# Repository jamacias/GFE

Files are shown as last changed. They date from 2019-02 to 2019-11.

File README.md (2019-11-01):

# GFE
Güimar Farm Explorer (GFE) is a low cost autonomous rover that aims at performing assisting and supervising remote farms.

The idea of the project is to be able to monitor a farm by commanding the robot to go to a certain known position and perform certain tasks of interest without having a human to be physically on site. Interesting uses may be related to crop health monitoring using NDVI images, apart from actually harvesting fruits (hopefully!).

The most recent version, iteration 2, is based on ["The bubble rebound obstacle avoidance algorithm"](https://ieeexplore.ieee.org/document/5524302). An array of ultrasonic sensors measure the distance to the objects and if any threat is detected the robot moves navigates on the direction with less density of obstacles. This project is designed to be used in semi-structured environments where the map and the way points that are (most probably) free of obstacles are known. The morphology and motion implemented kept in mind that it is designed to work in a winery with limited space, thus high agility is desired.

Please, refer to Thesis.pdf, images and the rest of the documentation inside the project itself for more information. Note that some of these are written in Spanish as this is the final project of my BSc. in Electronic Engineering. Nevertheless, all the source code is in English.

<p align="center">
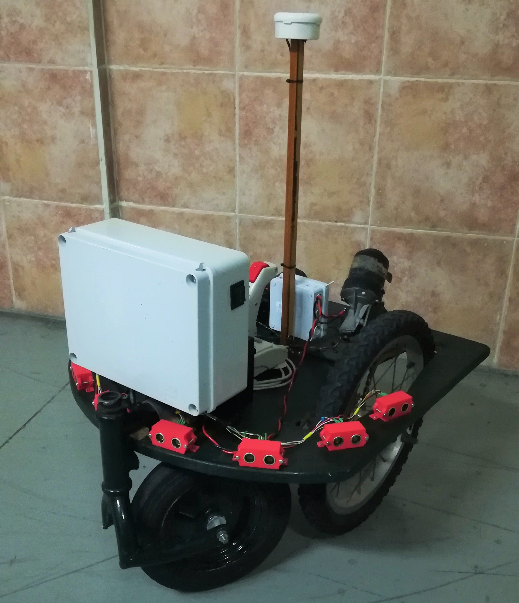
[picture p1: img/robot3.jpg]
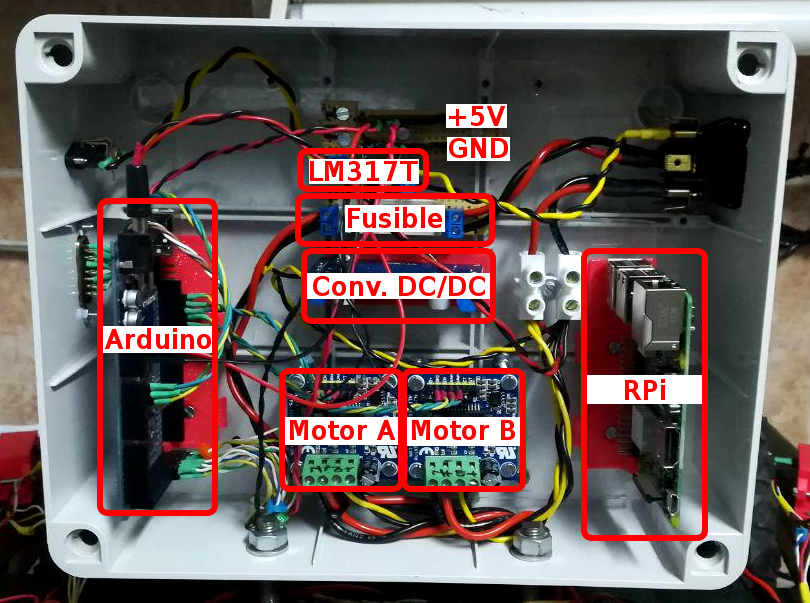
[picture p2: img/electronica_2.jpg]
     
</p>

## Main features:
- Manual control of the robot using diamond coordinates with a Quickshot QS-203 joystick.
- Autonomous navigation through waypoints marked.
- Obstacle avoidance.
- PI controller for the orientation of the robot.

## Known issues:
- Poor robustness on windy conditions - ultrasonic sensors are very sensible to this noise.
- Lack of sensor fusion for higher accuracy, nor Kalman filtering. Thus, kinematic equations are not really considered.
- Lack of encoders to compensate the shift between the wheels. This is compensated by transforming the system from MISO to SISO by using the orientation as the objective and setting the same values to both motors.
- No continuous trajectory is designed. The vehicle enters on either uses a PI controller to rotate to the correct orientation, or just moves forward in such direction. Considering the orography of the terrain where it was conceived, this might be a constraint anyway.

Even though these issues exist, the robot performs relatively well under certain conditions. It is able to navigate to the desired point with relatively good accuracy. The obstacle avoidance also works well under indoor conditions where the disturbance of the wind is minimal.

## BOM:
- Arduino MEGA 2560.
- Raspberry PI.
- 2x Windshield wiper DC motors (TGE5889A).
- 2x IMS-1 motor driver modules.
- 8x Ultrasonic sensors HC-SR04.
- 12V battery.
- LM317T voltage regulator.
- HMC5883L magnetometer.
- GY-GPS6MV2 GPS.
- Quickshot QS-203 joystick.
- Raspberry Pi NoIR camera.

## Libs:
- MOTOR (IMS-1 motor driver) - can be found in libs.
- TinyGPS.
- HMC5883_Simple.

## References:
[NDVI with RPi](https://github.com/robintw/RPiNDVI)

["The bubble rebound obstacle avoidance algorithm"](https://ieeexplore.ieee.org/document/5524302)

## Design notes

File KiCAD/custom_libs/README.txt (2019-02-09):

All libs are own-made except:

 -HC-SR04 https://github.com/adamclaassen/adamclaassen-kicad-parts (Modified: aesthetics)
 -ESP8266 https://github.com/jdunmire/kicad-ESP8266 (Modified: aesthetics)

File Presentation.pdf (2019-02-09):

# Diseño electrónico de un robot autónomo

## Trabajo de Fin de Grado

Javier Macías Solá
Universidad de La Laguna - GIEIA | Tutor: Dr. Leopoldo Acosta Sánchez

## Índice

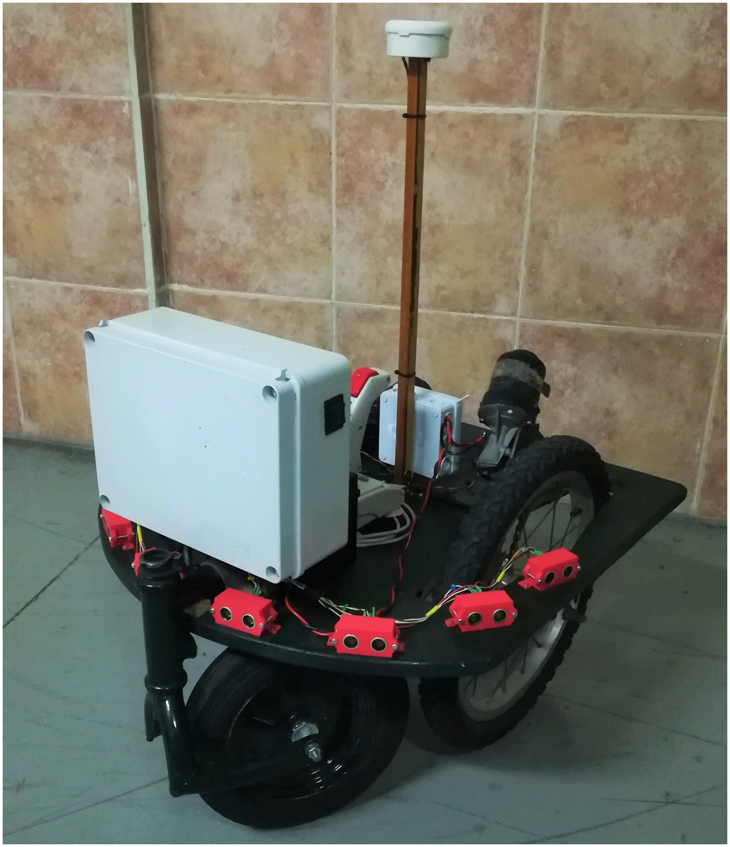
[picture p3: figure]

1. Introducción.
a. Objetivos.
b. Punto de partida.
2. Estudio previo y bases de diseño.
a. Concepto básicos de robots móviles.
b. Cinemática.
3. Electrónica. Sensores y actuadores.
4. Implementaciones.
a. Resumen versión 1.
b. Versión 2: modificaciones.
i. Estructura.
ii. Software.
5. Conclusions.

## Introducción

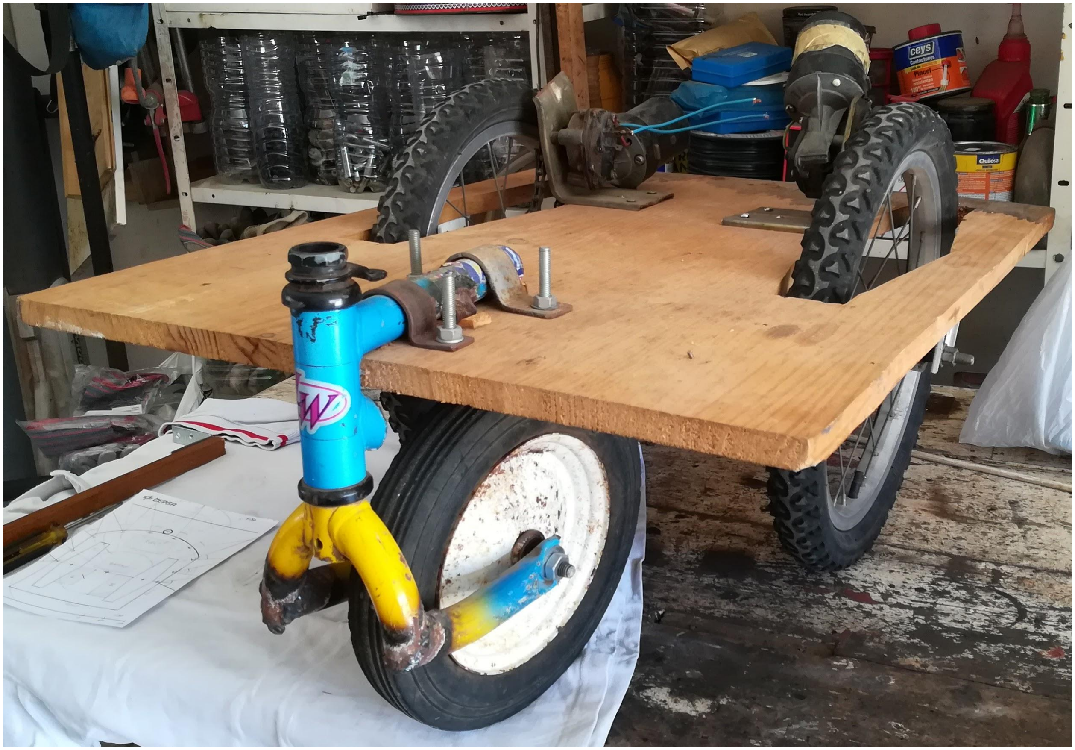
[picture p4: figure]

Idea: navegación autónoma entre los puntos marcados en un mapa desde una interfaz.

1. Objetivos básicos
a. Control autónomo y manual
b. Evitar obstáculos
2. Punto de partida
a. Base cuadrada (50 x 70 cm)
b. Dos ruedas diferenciales y una loca

# Estudio previo y bases de diseño

## Estudio previo

Robot móvil: tres grados de libertad (x, y, θ) con respecto al mundo global.

Navegación: conocer la ubicación actual, idear, y seguir una ruta.

1. Localización: ¿dónde está el robot?
a. Orientación limitada al rango [0, 360) grados.
b. Localización en grados decimales. Más cifras, más precisión y ruido.
2. Planificación: ¿ruta libre de obstáculos?

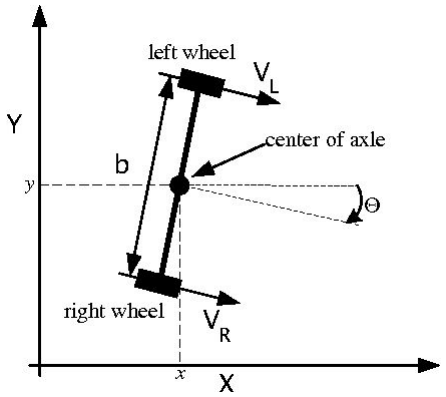
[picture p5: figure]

Fuente: Semantic Scholar

## Estudio previo

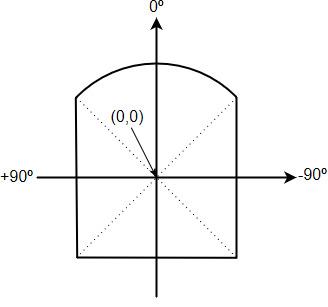
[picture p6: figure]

Coordenadas locales:

1. Origen en el centro geométrico.
2. Cero grados frente del vehículo, eje y. El signo del ángulo determina el lado.

¿Se puede ubicar un sensor?

Cinemática: depende de la velocidad y dirección de giro de las ruedas laterales.

## Bases de diseño

1. Maniobrabilidad
2. Detectar y evitar obstáculos
3. Poco volumen (radio < 1 m), pasillos de 1.40 m
4. Bajo costo/modular
5. Centro de gravedad bajo, estabilidad
6. Espacio para futuras mejoras
7. Escalabilidad

# Electrónica

Sensores y actuadores

## Electrónica general

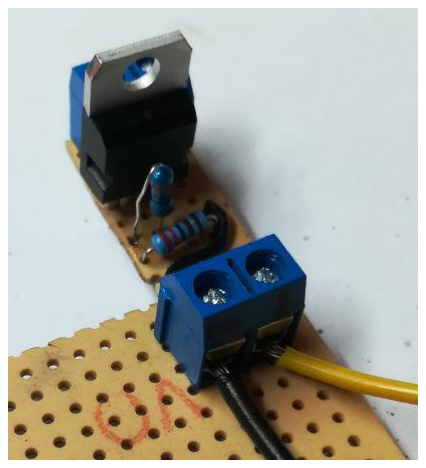
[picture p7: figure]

1. Batería: aporta la energía al sistema.
a. Reciclada de una moto.
b. Química: plomo ácido.
c. Seis celdas, 2.1 voltios por celda, 12.6 V total (OCV).
d. Ventaja: voltaje seguro y típico. En OCV representa el nivel de carga.
2. Cargador: fuente que permite recargar la batería.
a. Invierte la reacción química.
b. Plomo ácido: voltaje de carga entre 2.3 y 2.4 V/celda.
c. Reutilizada de un equipo de 17 V, adaptar el voltaje.
d. Polarizar un regulador (LM317T) a 13.8 V.
i. Dropout voltage ≈ 3.2 V.
ii. Intensidad máxima: 2.2 A.

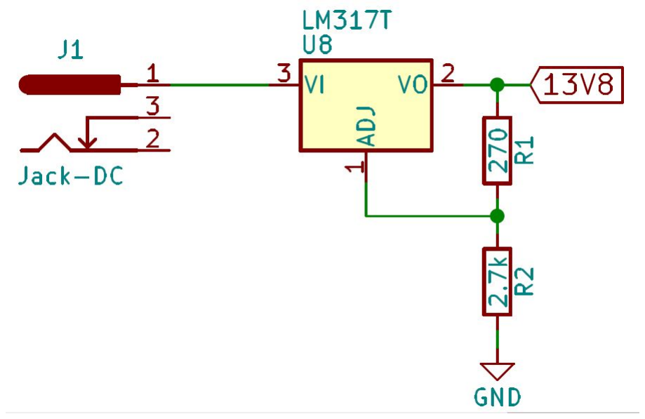
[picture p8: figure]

## Electrónica general

3. Controlador - Arduino MEGA 2560
a. Alimentación a 12 V con regulador integrado.
b. 4x Puertos Serial.
c. 2x I2C.
d. 15x PWM.
e. 16x Entradas analógicas.
f. 15x I/O digitales.
g. 10 bits ADC.
h. 8 bits DAC.
i. C/C++

No aporta potencia, hasta 20 mA/pin.

## Sensores

Permiten cerrar el lazo de realimentación del sistema.

1. Brújula: orientación del robot midiendo el campo magnético terrestre.
a. Orientación y ubicación críticas.
b. Separación de objetos metálicos (radio > 30 cm).
c. Librería: HMC5883_Simple.
d. Calibrar el módulo según la declinación magnética.
e. GY-271, magnetómetro HMC5883L
i. Alimentación a 5 V.
ii. Comunicación I2C.

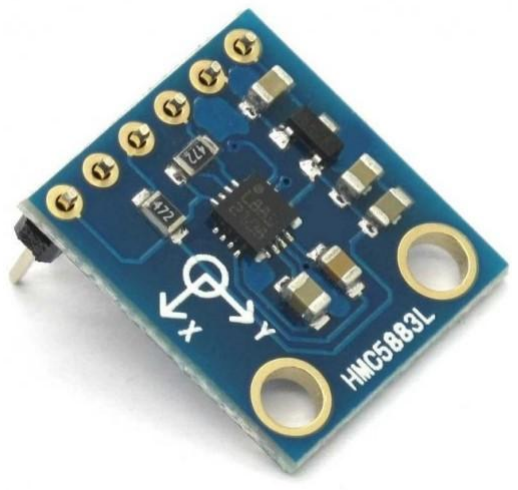
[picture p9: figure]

Fuente: njuskalo.hr

## Sensores

2. GPS: ubicación con respecto al mundo global.
a. Latitud (y) y longitud (x).
b. Librería: TinyGPS.
c. GY-GPS6MV2.
i. Alimentación a 5 V.
ii. Comunicación Serial.
d. Parsear sentencias típicas y estándar.
e. Señales débiles.

Fuente: dx.com

Ejemplo: $GPRMC,032606,A,3410.2358,N,11819.0865,W,0.0,207.2,180211,13.5,E,A*32

## Sensores

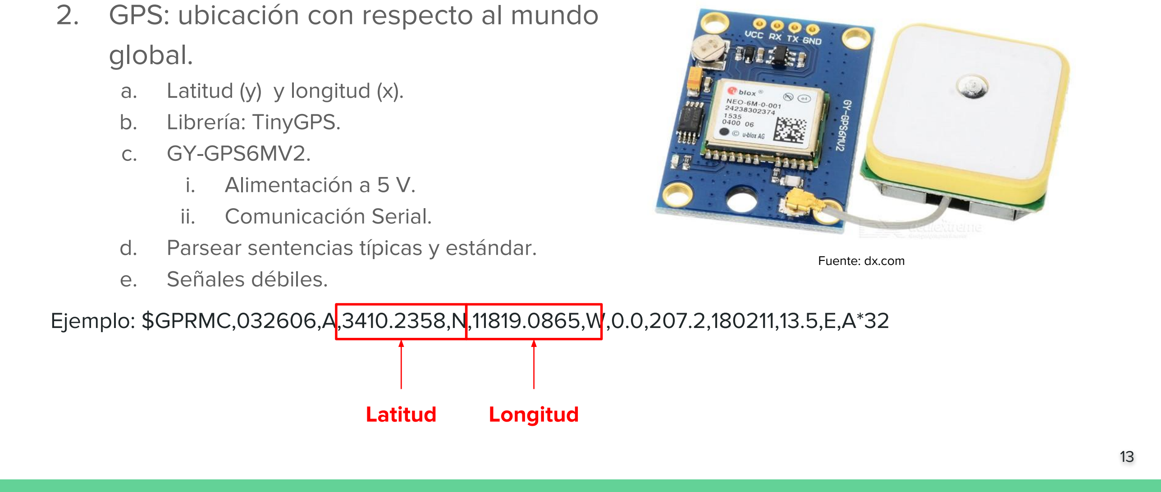
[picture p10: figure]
2. GPS: ubicación con respecto al mundo global.; a. Latitud (y) y longitud (x). b. Librería: TinyGPS. c. GY-GPS6MV2. i. Alimentación a 5 V.; Comunicación Serial.; e. Señales débiles.; Fuente: dx.com; Latitud; Longitud

d. Parsear sentencias típicas y estándar.

Ejemplo: $GPRMC,032606,A,3410.2358,N,11819.0865,W,0.0,207.2,180211,13.5,E,A*32

## Sensores

3. Ultrasonidos: detectar obstáculos.
a. Ventajas:
i. No hace falta librería. Función propia. ii. Económicos.
b. Desventajas:
i. Ondas de presión.
ii. | Eco
iii. | Escasa resolución espacial.
c. HC-SR04:
i. Alimentación a 5 V.
ii. | Comunicación por pines echo y trig.
iii. | Apertura de 15 grados.
iv. | Frecuencia máxima: 20 Hz

Fuente: amazon.co.uk

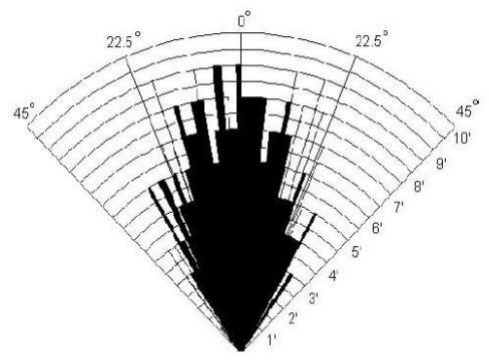
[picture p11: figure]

Fuente: [25]

## Sensores

4. Joystick: control manual del operario.
a. Manejo intuitivo.
b. Dos potenciómetros que marcan cada eje.
c. Adaptar Quickshot QS-203:
i. Potenciómetros polarizados a 5 V y lectura del valor analógico.
ii. | Pull-up resistors para los botones.
iii. | Trimado.
iv. | Mantener el conector DA-15.

## Adaptación joystick

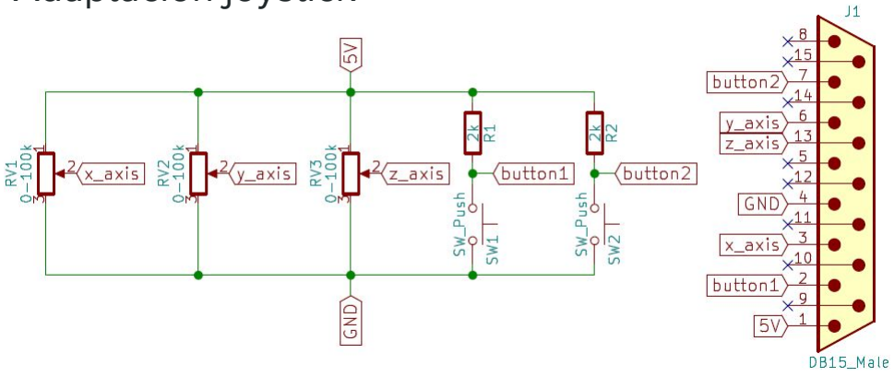
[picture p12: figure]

## Actuadores

1. Motores: cambian la pose del vehículo.
a. TGE589A. Motor de limpiaparabrisas.
i. DC, velocidad proporcional al voltaje.
ii. | Tornillo sin fin, par alto (18.3 Nm).
iii. | Consumo: 0.9 A con poca carga.
iv. | Intensidad de cortocircuito: 12 A.
v. Velocidad angular: 66 rpm.
b. Desventajas: falta de documentación.
c. Reductora externa de 8/16.

Suponiendo correctos los datos anteriores: hasta 176 kg con dos motores.

Fuente: rctankcombat.com

Solución: puente H excitado con PWM.

Módulo IMS-1

a. Hasta 50 A.
b. Velocidad de 8 bits (DAC Arduino).
c. Librería: MOTOR.

## Problema: voltaje intermedio en un sistema digital

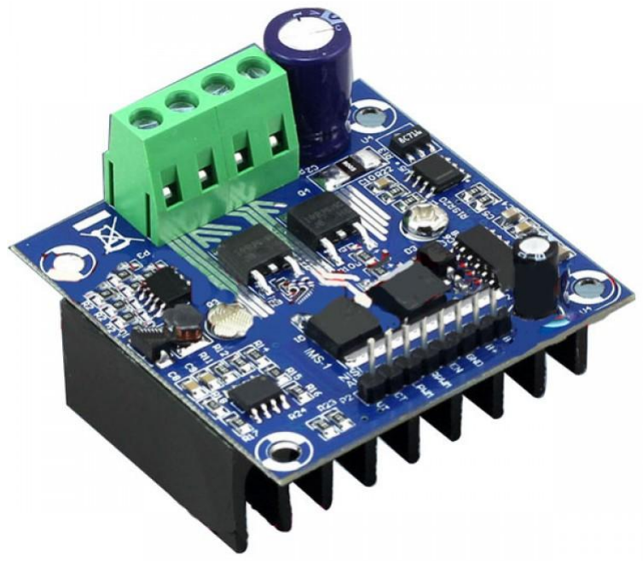
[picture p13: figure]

Fuente: thanksbuyer.com

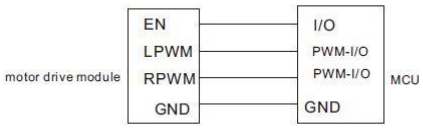
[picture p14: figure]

Fuente: [10]

# Implementaciones

Centrada en implementar los componentes.

a. Modo automático:
i. Orientado a seguir un rumbo y evitar paredes.
ii. | Cuatro sensores ultrasonidos.
iii. | Controlador todo/nada.
b. Modo manual:
i. Algoritmo: transformar coordenadas cartesianas a
| diamante y comandar los motores.
c. Problemas:
i. Orientación y comunicación remota poco robusta. ii. Inercia. Centro de gravedad desplazado.

## Resumen versión 1

## Resumen versión 1

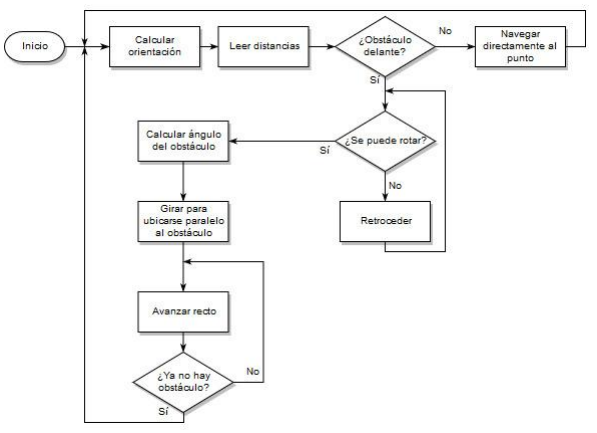
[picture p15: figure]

## Resumen versión 1

Algoritmo modo manual: transformar coordenadas cartesianas a diamante [23].

## Resumen versión 1

## Resumen versión 1

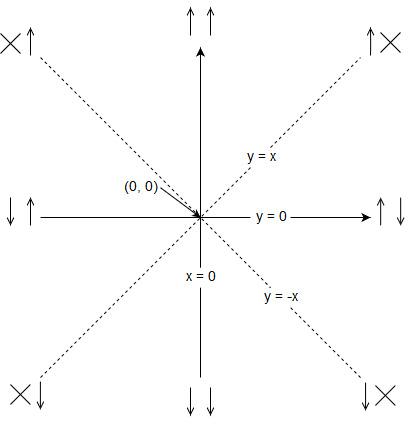
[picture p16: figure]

## Resumen versión 1

Fuente: [23]

## Resumen versión 1

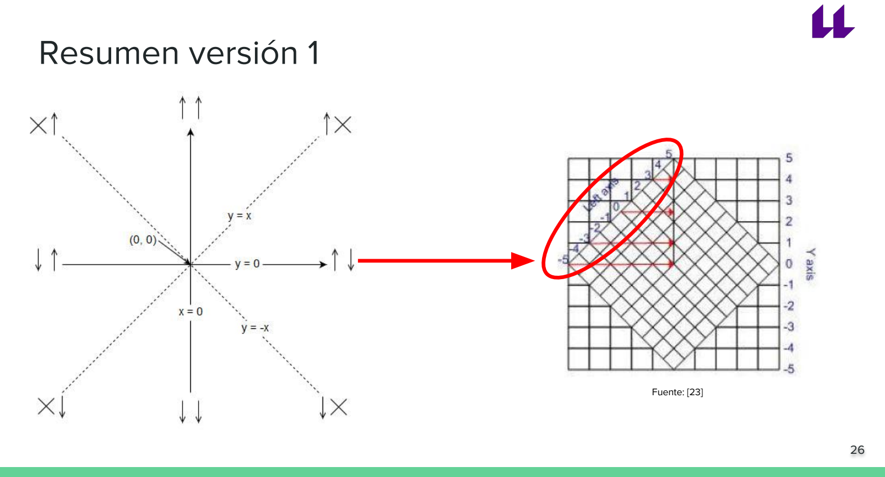
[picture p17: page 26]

Fuente: [23]

Implementar navegación y evitar obstáculos.

1. Electrónica jerárquica: multi-threading.
2. Centro de gravedad menos desplazado.
3. “The bubble rebound obstacle avoidance algorithm” [22].
4. Protecciones para sensores y nuevas ubicaciones.
5. Controlador PI.

## Versión 2: modificaciones

## Versión 2: electrónica

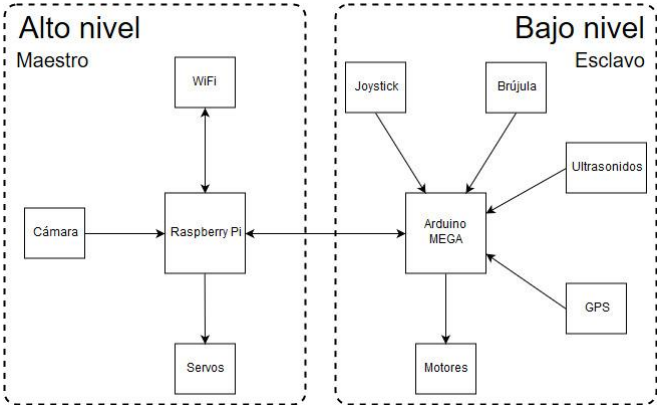
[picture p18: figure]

## Versión 2: electrónica

1. Brújula.
2. Joystick.
3. Motores.
4. GPS.
5. Interruptor de tres estados.
6. Batería.
7. Interfaces de comunicación.
8. Resto de electrónica.
9. Array de ultrasonidos.

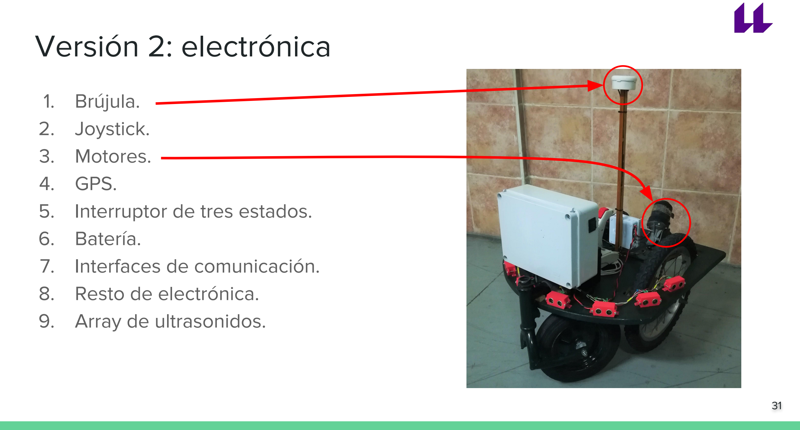
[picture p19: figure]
Versión 2: electrónica; 1. Brújula. 2. Joystick. 3. Motores. 4. GPS. 5. Interruptor de tres estados. 6. Batería. 7. Interfaces de comunicación. 8. Resto de electrónica. 9. Array de ultrasonidos.

## Versión 2: electrónica

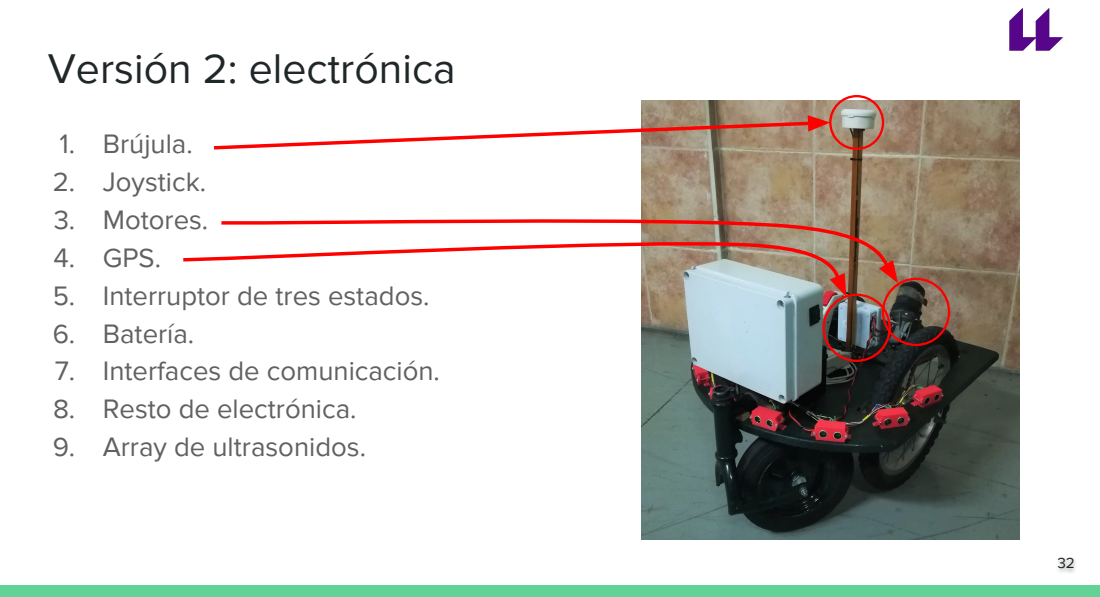
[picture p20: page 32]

1. Brújula.
2. Joystick.
3. Motores.
4. GPS.
5. Interruptor de tres estados.
6. Batería.
7. Interfaces de comunicación.
8. Resto de electrónica.
9. Array de ultrasonidos.

## Versión 2: electrónica

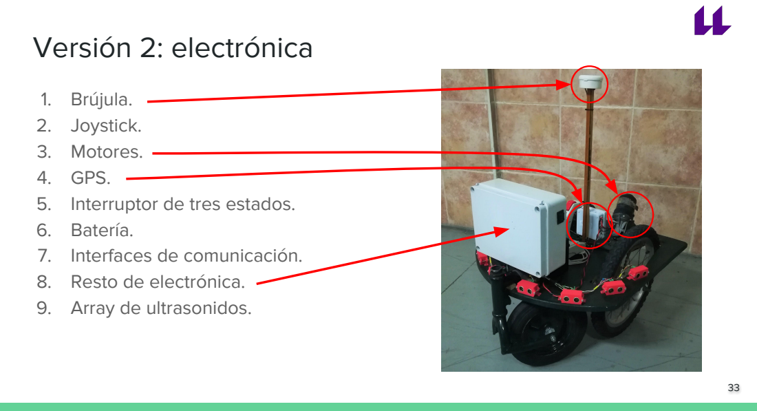
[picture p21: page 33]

1. Brújula.
2. Joystick.
3. Motores.
4. GPS.
5. Interruptor de tres estados.
6. Batería.
7. Interfaces de comunicación.
8. Resto de electrónica.
9. Array de ultrasonidos.

## Versión 2: electrónica

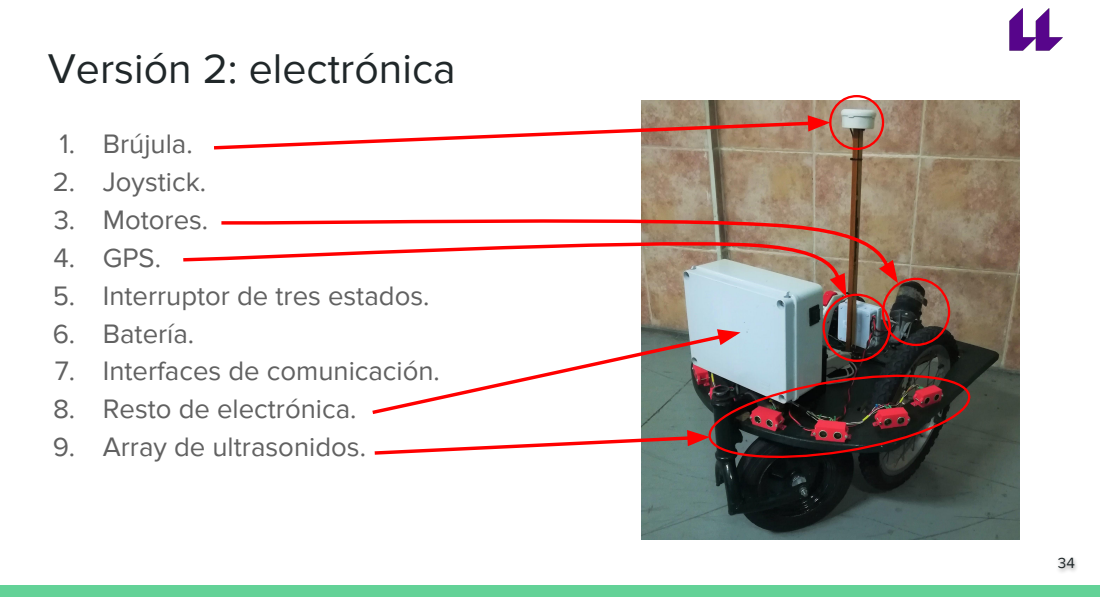
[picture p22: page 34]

1. Brújula.
2. Joystick.
3. Motores.
4. GPS.
5. Interruptor de tres estados.
6. Batería.
7. Interfaces de comunicación.
8. Resto de electrónica.
9. Array de ultrasonidos.

## Versión 2: electrónica

DC jack cargador.

Conector DA-15 (joystick).

Gestionar la comunicación remota. Alto nivel.

1. AP para conexión SSH.
2. Tiempo de arranque lento.
3. GPIOs configurados en boot (bash).
4. Alias de Linux para cambiar el estado.
5. Comunicación Serial con Arduino (debug).

Versión 2: software. Raspberry Pi.

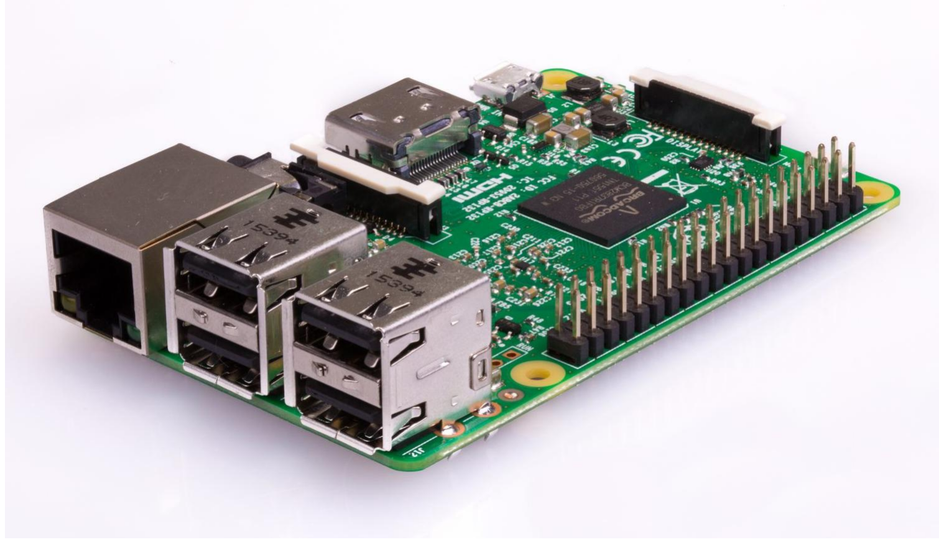
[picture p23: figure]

Fuente: raspberrypi.org

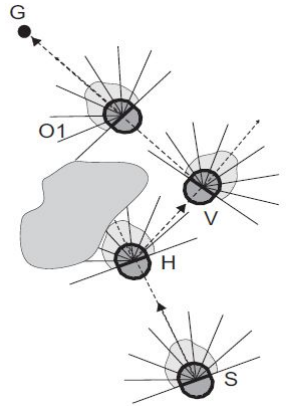
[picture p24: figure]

Gestionar el nivel más bajo de comunicación.

Tras confirmar que la Raspberry Pi está lista:

1. Navegar en campo abierto.
2. Evitar obstáculos (bubble rebound algo.)

Versión 2: software. Arduino.

Original | Implementación
Lógica | Difusa | Booleana
Burbuja | Variable con la cinemática | Fija

1. Ultrasonidos cubren 180 grados.
2. Si detecta que puede golpear, rebota hacia la menor densidad de obstáculos.
3. Navega recto hasta que el objetivo esté visible.
4. Si el objetivo está visible, navega directamente el punto.

## The Bubble Rebound algorithm. Resumen

Versión 2: software. Arduino.

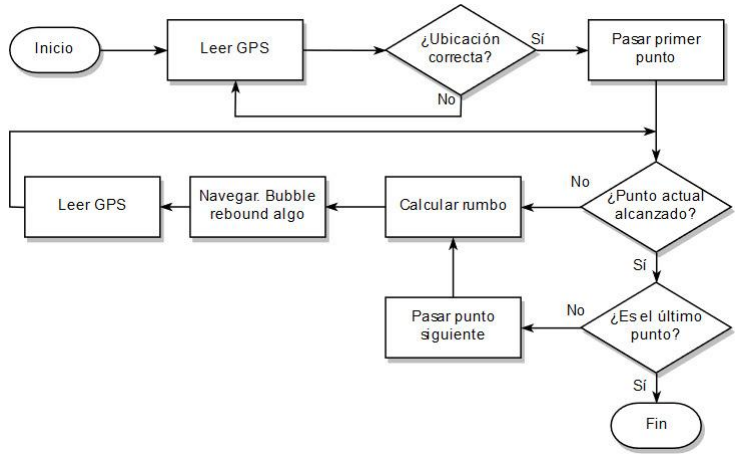
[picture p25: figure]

1. Rotar sobre sí mismo. Controlador PI.
a. Parte proporcional con el incremento de la variable de proceso [12, pp. 52-78].
b. Error sólo en la parte integral.
2. Mover hacia delante. Todo-nada calibrado para corregir la deriva.

Versión 2: software. Arduino.

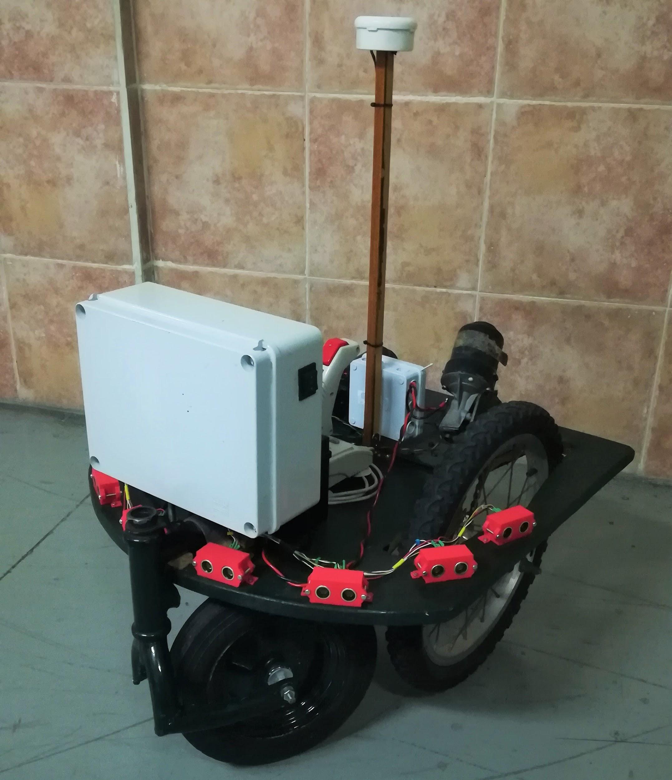
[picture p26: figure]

# Conclusions

Sensor location and filtering. PI over bang-bang controller. Hierarchical structure.

## ¡Gracias por su atención!

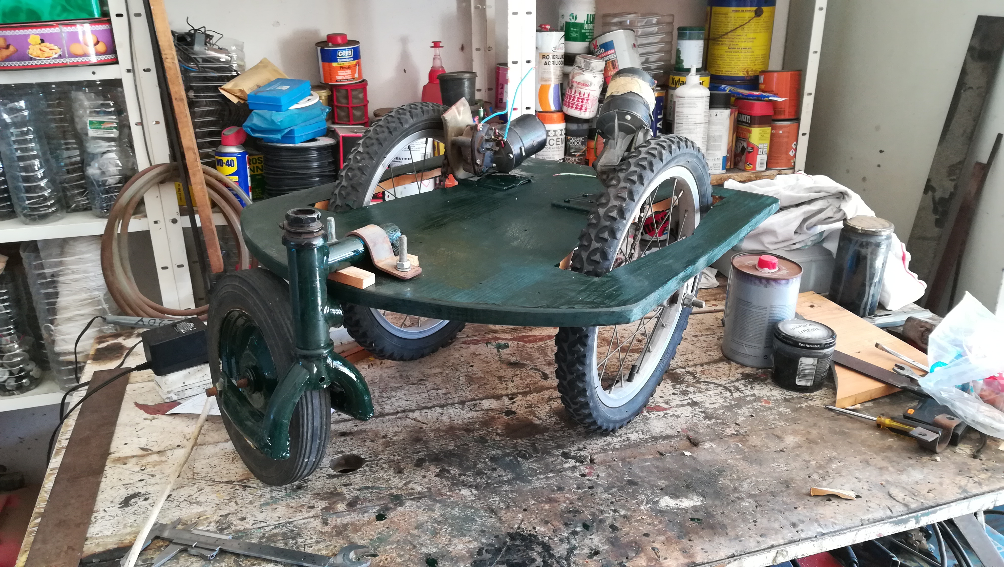
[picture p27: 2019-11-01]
img/robot2.jpg

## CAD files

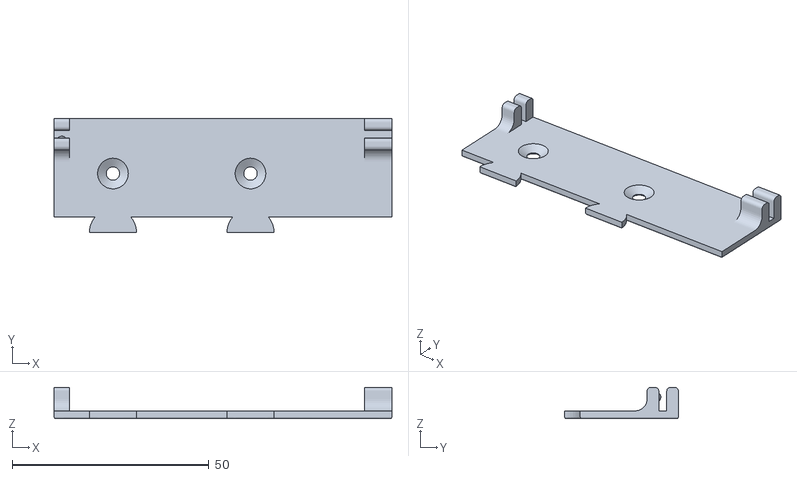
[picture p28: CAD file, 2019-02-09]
3D Models/arduino_support.stl
86.0 x 29.0 x 8.00

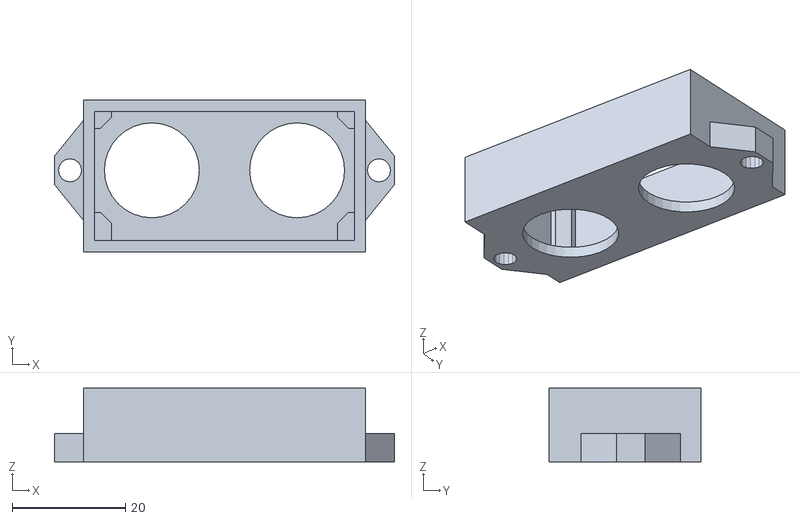
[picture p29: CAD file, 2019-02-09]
3D Models/HC-SR04/case_top.stl
60.0 x 26.8 x 13.0

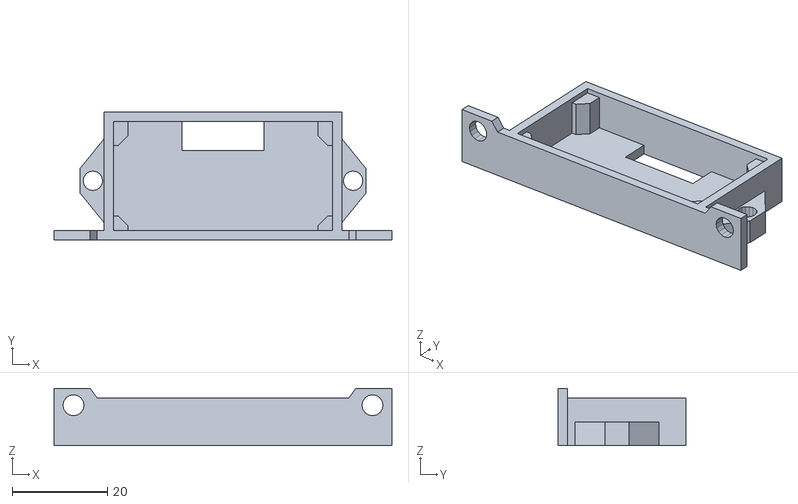
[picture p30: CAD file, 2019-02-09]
3D Models/HC-SR04/case_bot.stl
70.8 x 26.8 x 12.0

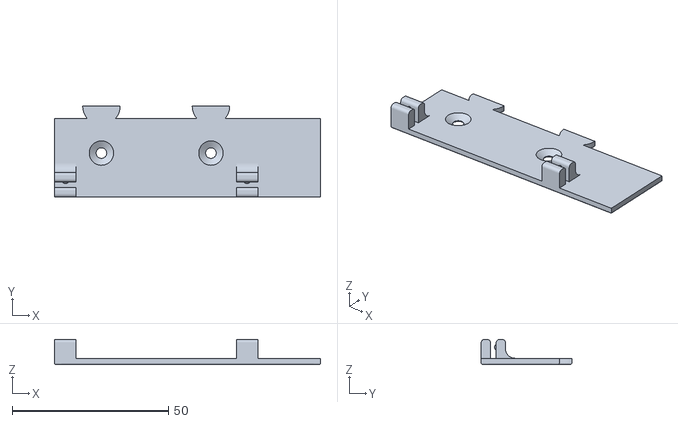
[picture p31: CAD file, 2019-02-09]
3D Models/rpi_support.stl
85.0 x 29.0 x 8.00

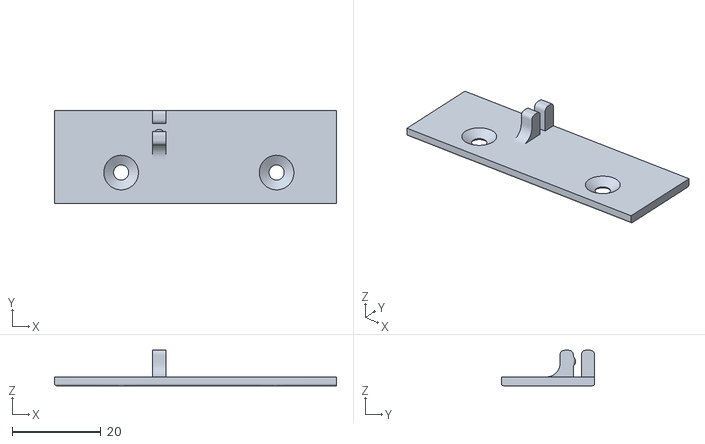
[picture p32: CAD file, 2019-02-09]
3D Models/dc_dc_converter.stl
63.5 x 21.0 x 8.00

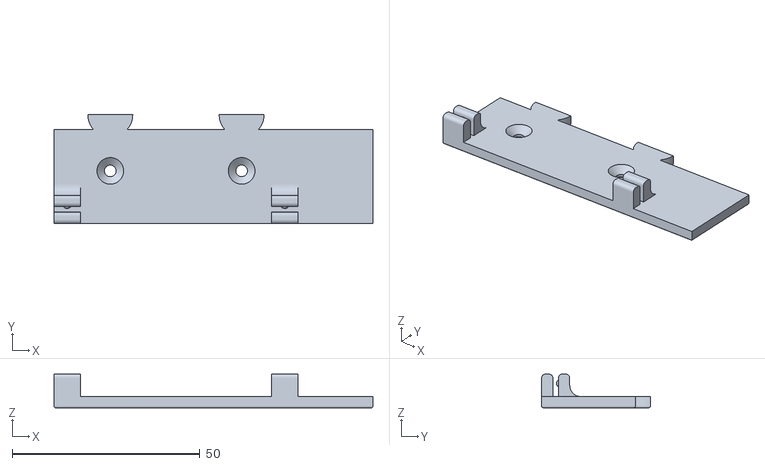
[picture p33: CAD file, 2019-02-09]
3D Models/Startmodul.stl
85.0 x 29.0 x 9.00

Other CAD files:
Blueprints/iter_2.dwg
Blueprints/inventor_drawing_template.dwg
Blueprints/case_top.dwg
Blueprints/plantilla_ESIT.dwg
Blueprints/plantilla_inventor.dwg
Blueprints/cajetin.dwg
Blueprints/case_bot.dwg
Blueprints/dc_dc_support.dwg
Blueprints/arduino_support.dwg
Blueprints/iter_1.dwg
Blueprints/rpi_support.dwg
Blueprints/OldVersions/plantilla_inventor.0001.dwg
3D Models/HC-SR04/case.blend
3D Models/HC-SR04/case_bot.ipt
3D Models/HC-SR04/case_top.ipt
3D Models/Imported Components/arduino_support/arduino_support.ipt
3D Models/Imported Components/dc_dc_converter/OldVersions/dc_dc_converter.0001.ipt
3D Models/Imported Components/dc_dc_converter/dc_dc_converter.ipt
3D Models/arduino_support.blend
3D Models/dc_dc_converter.blend
3D Models/rpi_support.blend
3D Models/rpi_support.obj
Blueprints/OldVersions/inventor_drawing_template.0001.dwg
Documentation/Video_TFG.blend

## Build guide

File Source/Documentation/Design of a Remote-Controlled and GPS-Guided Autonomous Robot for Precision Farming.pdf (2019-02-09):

ARTICLE

International Journal of Advanced Robotic Systems

# Design of a Remote-controlled and GPS-guided Autonomous Robot for Precision Farming

Regular Paper

İlker Ünal¹* and Mehmet Topakci²

1 Technical Science Vocational School, Akdeniz University, Antalya, Turkey
2 Department of Agricultural Machinery and Technologies Engineering, Faculty of Agriculture, Akdeniz University, Turkey *Corresponding author(s) E-mail: ilkerunal@akdeniz.edu.tr

Received 26 January 2015; Accepted 28 November 2015

DOI: 10.5772/62059

© 2015 Author(s). Licensee InTech. This is an open access article distributed under the terms of the Creative Commons Attribution License (http://creativecommons.org/licenses/by/3.0), which permits unrestricted use, distribution, and reproduction in any medium, provided the original work is properly cited.

Abstract
Determining variations in fields is important for precision farming applications. Precision farming is used to deter‐ mine, analyse, and manage factors such as temporal and spatial variability to obtain maximum profit, sustainability, and environmental protection. However, precision farm‐ ing is excessively dependent on soil and plant test process‐ es. Furthermore, test processes are time-consuming, laborious and expensive. These processes also cannot be performed quickly by humans. For these reasons, autono‐ mous robots should be designed and developed for the detection of field variations and variable-rate applications. In this study, a remote-controlled and GPS-guided auton‐ omous robot was designed and developed, which can be controlled via the 3G internet and is suitable for image-processing applications. The joystick is used to manually remotely control the robot movements in any direction or speed. Real-time video transmission to the remote comput‐ er can be accomplished with a camera placed on the vehicle. Navigation software was developed for steering the robot autonomously. In the results of the field test for the navigation software, it was found that the linear target point precision ranged from 10 to 12 cm and the distributed target point precision ranged from 15 to 17 cm.

Keywords Remote Control, GPS-guided Robot, Naviga‐ tion, Precision Farming, 3G Internet

### 1. Introduction

Agricultural practices have been revolutionized by the introduction of computers and electronic components. One example is automatic navigation of agricultural machines, including tractors and combine harvesters. GPS and machine vision techniques find many applications in agricultural production practices [1]. The developments of electronics and the resulting decrease in the size of com‐ puters, and the simultaneous development of smarter chips and microprocessors, have greatly affected the agricultural industry. Improvements in data acquisition and transfer and the processing power of computers, as well as their ability to process huge quantities of data in very little time, have contributed to the increase in autonomous vehicle research [2]. The potential benefits of automated agricul‐ tural vehicles include increased productivity and accuracy, together with enhanced operational safety. Research on autonomous agricultural vehicles has become very popu‐

Int J Adv Robot Syst, 2015, 12:194 | doi: 10.5772/62059 1

lar, and the robotics industry has developed a wide range of remarkable robots. In the near future, farmers will be using affordable, dependable autonomous vehicles for agricultural applications [3].
The historical development of the automatic tractor can be dated back to the early 20th century. The first steering attachment for tractors was developed in 1924 [4]. Most agricultural machines that moved autonomously used mechanical settings until the 1970s. In the 1980s the potential for combining computers with image sensors provided opportunities for machine vision-based guidance systems [5]. Within 10 years, machine vision was being used to successfully guide agricultural tractors in the field [6, 7]. Around 1990, the Global Positioning System (GPS) became available in a limited capacity for civilian use, and the possibility of rapid and accurate vehicle location and navigation sparked a flurry of activity. In 1995, the system reached full operational capability; since that time, GPS has had a significant effect on agricultural practices [8]. In 1997, agricultural automation became a major issue, along with the advocacy of precision agriculture. Since 2000, drawing on developments in sensor and GPS technology, research‐ ers have shown maintained interest in autonomous farm machinery.
Many research institutions have recently developed robot tractors and robot vehicles for agricultural purposes [9]. In
[10] a sensor fusion technique for navigational posture estimation was developed for a skid-steered mobile robot vehicle in nursery tree plantations. In [11] an automated rice transplanter and autonomous guidance operation were developed. In [12] the authors developed a low-cost and small-scale electronic robot vehicle and automatic guidance system for orchard application. Another autono‐ mous robot for use in orchards was developed in [13]: this vehicle is able to autonomously drive through tree rows. The researcher reported that the five vehicles completed so far have travelled autonomously over 300 km in research and commercial tree-fruit orchards; preliminary results in time trials conducted by extension educators indicate efficiency gains of up to 58%. Much further research has been performed towards the development of agricultural robot and semi-robot vehicles [14-20].
However, no study has yet reported on an autonomous vehicle that is both GPS-guided and remote-controlled, and which can be controlled via the internet for field applica‐ tions. This study addresses this research gap (Figure 1). Navigation software is also developed for steering the robot autonomously.

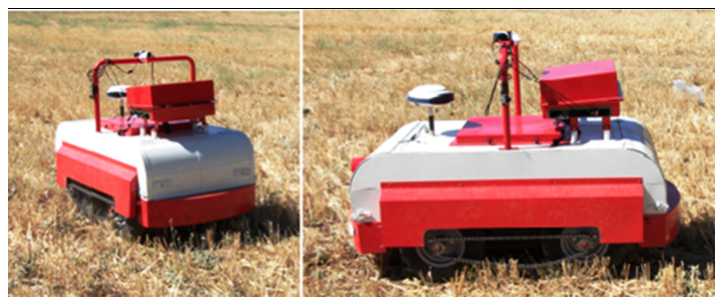
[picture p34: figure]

Figure 1. Remote-controlled and GPS-guided autonomous robot

### 2. Design of the autonomous robot

The designed robot is able to steer point to point both autonomously and under manual control. The robot involves five main sections:
- Mechanical design and steering mechanism: An agricul‐ tural robot platform was developed to achieve the goal of both remote-controlled and autonomous navigation. The robot chassis, wheel module, and method of power are explained in this section.
- Motor control mechanism: The mobile robot is a four-wheel robot which steers with two DC motors. The differential steering method is used. The DC motor controller and motor control algorithm are explained below.
- Remote control algorithm: The joystick is used to manually remotely control the robot movements in any direction or speed. The data flow mechanism between the robot and the remote computer via the internet is explained in detail below.
- Autonomous guidance algorithm: The GPS-guided robot is designed to operate in open field conditions. The GPS data processing and navigation algorithm are explained in this section, below.
- Software development: Client-server software was developed to control all the functions in the robot. The running mechanism of the software is explained below.

2.1 Mechanical design and steering mechanism
The designed robot is shown in Figure 2. The robot chassis was made of U-steel profile, and the body structure covered with sheet metal with a thickness of 2 mm. The robot was powered by two 24 V – 0.5 kW – 1440 rpm DC motors. Two reducers with 1:30 transmission rate were used to reduce rpm and increase torque. Four 4.00x8 agricultural rubber wheels were chosen to operate in open field conditions.

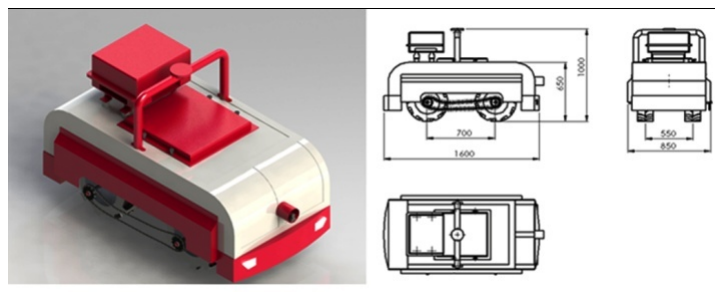
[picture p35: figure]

Figure 2. Designed robot views
The DC motors and the front wheels were coupled to the reducers. The rear wheels were linked to each other with the help of the bearing shaft. A chain sprocket was mounted on each wheel, and the wheels on the right side and the left side were linked by the chain. This provided the differential steering mechanism (Figure 3). The steering system worked as follows: if the two motors rotate at the same speed, the robot moves forward or backward; if there is a difference between the speeds of the two motors, the robot steers in the direction of the slower motor.
2 Int J Adv Robot Syst, 2015, 12:194 | doi: 10.5772/62059

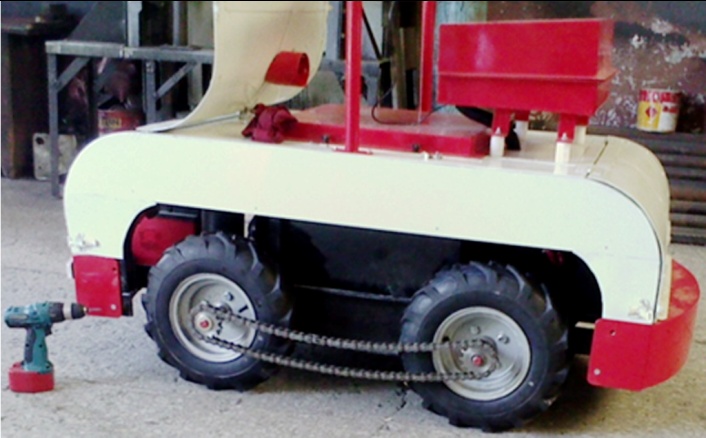
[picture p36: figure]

Figure 3. Designed robot views
Energy input for the electronic components and the motors was provided by three 12 V, 72 Ah rechargeable mainte‐ nance-free sealed batteries. For the motors, two batteries were connected in series to provide 24 V. The other battery was connected to a DC/AC inverter. A 12 V DC/AC inverter was used for the charge of the robot computer. The robot was able to continuously operate for six hours in the field. It weighed 250 kg and payload was approximately 900 kg. The reducer torque was calculated for each wheel accord‐ ing to Equation 1. The maximum robot speed was approx‐ imately 3.8 km/h (Equation 2).
( ) | *9550 ( ) | 99.5
( / | )

Motor Power kW
Reducer torque Nm | Nm Reducer Speed rev min = | = | (1)

With an 8” rim, the outside diameter of the wheel was approximately 440 mm. At a rated speed of 48 rev/min, the following vehicle speed was obtained:

( | ) | ( ) | ( ) ¹ | . | 3.14 60
/ | 3.8 / 1000
Shaft Speed min xTire dia m x | x v km h | km h ⁻ = | = | (2)

The shaft torque can be calculated by Equation 3:

0.085 | . | 9.8 ( ) | ( ) | 45.8
2
xWeight kg xTire dia m x Shaft torque | Nm = | = | (3)

The rolling resistance is very hard to determine. In the literature, rolling resistance coefficient = 0.085 is suggested for off-road (unpaved surface) applications.
The developed robot was used to determine and map the stubble density ratio of a field using the online image-processing method. A Canon PowerShot SX100 IS digital camera mounted in a sealed box on the autonomous robot was used to obtain stubble images in the field. The base area of the sealed box was 45x50 cm. The digital camera was placed at a height of about 60 cm above the soil surface. The autonomous robot for stubble density measurement is shown in Figure 4.

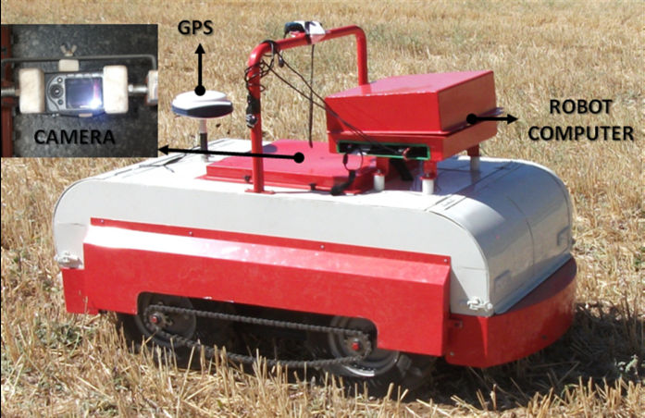
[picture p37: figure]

Figure 4. Developed robot for stubble density measurement

2.2 Mobile robot kinematics
The designed robot was assumed to be a nonholonomic system. Control of nonholonomic systems is theoretically challenging and practically interesting [21]. Although every nonholonomic system is controllable, it cannot be stabilized to a point with pure smooth (or even continuous) state feedback law because of Brockett’s Theorem [22]. In order to overcome this difficulty, a variety of sophisticated feedback stabilization methods have been proposed by [21, 23-24].
To characterize the current localization of the mobile robot in its operational space of evolution on a 2D plane (x, y), we must first define its position and its orientation. Assume the angular orientation (direction) of a wheel is defined by angle θ between the instant linear velocity of the mobile robot v and the local vertical axis, as shown in Figure 5.

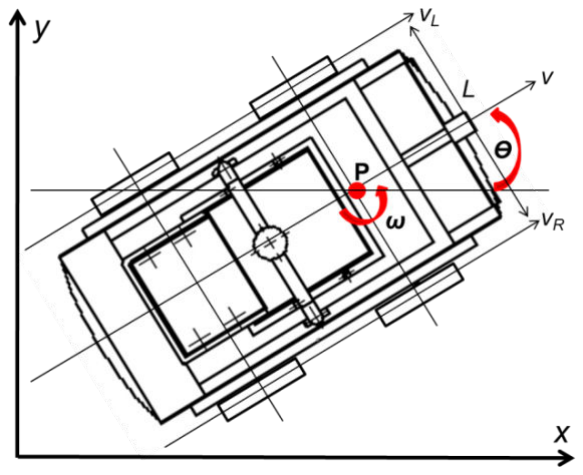
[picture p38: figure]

Figure 5. The kinematics of the mobile robot
The translational velocities of the left and right wheels are obtained by vL

= ωmlr/g and vR = ωmrr/g, where ωml and ωmr are angular speeds of the left and right drive motors, r the radius of the drive wheel, and g the reduction ratio of the reducer. The centre point P of the axle of the driving wheels

İlker Ünal and Mehmet Topakci: 3 Design of a Remote-controlled and GPS-guided Autonomous Robot for Precision Farming

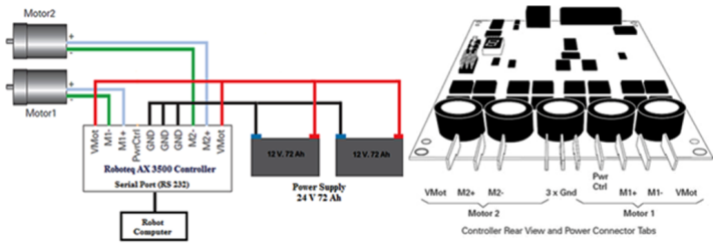
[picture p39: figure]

is defined as the reference point of the mobile robot position. The forward linear velocity v and angular speed ω at the point P can be described in the moving frame as follows:

2

R | L v v v | + = | (4)
R | L v v
L w | - = | (5)

where L is the distance between the two drive wheels. In the base frame, the kinematic model of the differential drive mobile robot can be expressed as:

0
0
0 1
x | cos | v y | sin
q
q | w q
æ ö æ | ö ç ÷ ç | ÷æ ö
ç ÷ ç | ÷ = | ç ÷
ç ÷ ç | ÷è ø è ø è | ø

&
&
& | (6)

where x, y, and θ are the positions and orientation of the robot and x˙, y˙, and θ˙ are their derivatives, representing the velocities and angular speed of the vehicle, respectively.

2.3 Motor control mechanism

A Roboteq AX3500 (Roboteq Inc., Arizona, USA) motor controller with two channel outputs was used to power and steer the robot by varying the speed and direction of the motors at each side of the chassis. The controller’s two channels can be operated independently or combined to set the forward/reverse direction and steering of a robot by coordinating the motion on each side. The controller was designed to interface directly to high-power DC motors in computer-or remote-controlled mobile robotics and automated robot applications. The motors were driven using high-efficiency power MOSFET transistors control‐ led using Pulse Width Modulation (PWM) at 16 kHz. The AX3500 power stages can operate from 12 to 40 VDC and can sustain up to 60 A of controlled current, delivering up to 2400 W (approximately 3 HP) of useful power to each motor. The AX3500 motor controller was connected to the robot PC via its RS232 port. This connection can be used to both send commands and read various status information in real time from the controller. RS232 commands were very precise and securely acknowledged by the controller. The motor control mechanism block schema is given in Figure 6.
Motor control software was developed for communication between the AX3500 controller and the robot computer. The robot computer’s serial port was set as follows: 9600 bits/s, 7-bit data, 1 Start bit, 1 Stop bit, Even Parity. After connection, the controller was always ready to receive data and could send data from developed software at any time. The AX3500 used hexadecimal notation for accepting and responding to numerical commands. AX3500 motor control commands were composed of a series of four characters (Table 1). Motor speed value was sent from 00 to 7F in the forward or reverse direction for a given channel. These commands were sent to steer the robot both man‐ ually (joystick) and autonomously from the computer serial port using the developed software.

Control
Sign
Command | Speed
Motor 1 Motor 2 | Motor 1 | Motor 2
Motor
Forward

!A00 – 7F !A7F ↑ !A3F ↑ Forward-Fast Forward-Slow

Motor Reverse !a00 – 7F !a3F ↓ !A7F ↑ Reverse-Slow Forward-Fast
Motor Stop !A00 or !a00 !A00 | !a3F ↓ | Stop | Reverse-Slow
Table 1. Motor speed commands and examples

2.4 Remote control algorithm
A Logitech Attack 3 joystick was used to control the robot. The joystick interfaced through a standard USB type-A connector to the remote computer. Software was developed to read the value of the two axes, and caused the robot to move accordingly. The y-axis controlled the forward-reverse movement of the robot, while the x-axis controlled the rotation left and right. Multiple button inputs could be configured for a variety of tasks. The program received x, y, and z values ranging from 0 to 65536 and also button values ranging from 1 to 11. Both axes were made propor‐ tional such that the speed of movement increased as the joystick moved a greater distance from the origin. Com‐ mands sent from the joystick were passed on by the remote computer at 10 ms intervals. Joystick commands are shown in Table 2.

Figure 6. Motor control mechanism block schema

Control | Y-Axis | | X-Axis
| Forward | Reverse | Right | Left
Joystick | 32769 - 65536 | 0 - 32767 | 32769 - 65536 | 0 - 32767
Table 2. Joystick commands

There were some mismatches between motor-speed commands and joystick commands. For this reason, joystick commands were converted to motor-speed commands by the client software on the remote computer. The conversion table is given in Table 3. The buttons on the base of the joystick were assigned the following functions. Button 1 was emergency stop, which halted the system completely, requiring a restart both in autonomous and manual mode. Button 11 selected autonomous robot steering mode. Other buttons selected manual robot steering mode. The flow chart of the remote control algorithm of the robot is shown in Figure 7.

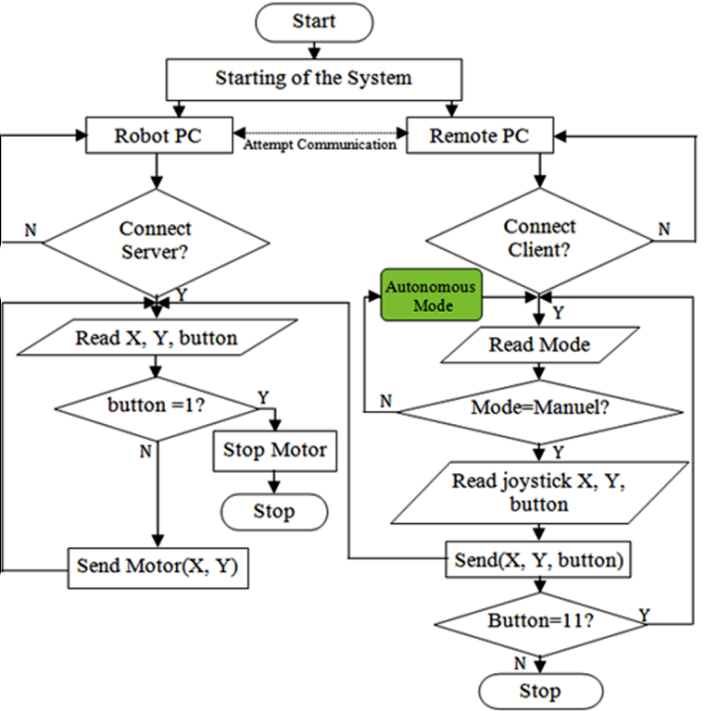
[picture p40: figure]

Figure 7. Robot remote control algorithm

2.5 Autonomous guidance algorithm
A Promark 500 GPS (Magellan Co., Santa Clara, CA, USA) receiver was used to navigate the robot. The receiver had 75 channels and up to 20 Hz data output rate. It was the most flexible GNSS (Global Navigation Satellite Systems) surveying system available, offering multiple operating modes, configurations and communication modules (UHF,

GSM/GPRS, EDGE) and protocols. It was connected to Corse-TR (Continuously Operating Reference Stations-Turkey) via a phone data card (SIM Card) to receive correction signals. The receiver had a 99% confidence interval. The accuracy of the position obtained varied (according to the manufacturer‘s data) from below 10 mm with correction signals. The receiver had RS-232, Bluetooth, and USB ports to allow National Marine Electronics Association (NMEA) 0183 data transfer to a robot comput‐ er. Data such as the geographical coordinates and advance speed of the spot being measured were then sent to the serial port of the robot computer. The RS-232 serial com‐ munication protocol was used for two-way communication between the GPS receiver and the robot computer using the serial data cable of the GPS receiver. The GPS receiver installation data were sent to set up the GPS receiver via the server software [25].
In the robot, GPS receivers sent data on latitude, longitude, speed, time, etc., by cable to other electronic devices via the RS-232 serial port. NMEA 0183 was the standard protocol used by GPS receivers to transmit data. NMEA 0183 sentences were all American Standard Code for Informa‐ tion Interchange (ASCII). Each sentence was initiated with a dollar sign ($) and the next five characters determined the sentence type. The $GPRMC sentence type was the most useful format, and included positional and temporal data. The GPS receiver sent data every 10 ms to the software. The communication speed was set at 9600 baud. $GPRMC sentence fields were separated with commas. In the first step the sentence was stored in an array variable by the software; in the second step sentence fields were split by a Split command in the software, and in the third step positional data were converted to UTM (Universal Trans‐ verse Mercator) format and sentence fields stored to the SQL Server 2005 database (Figure 8).

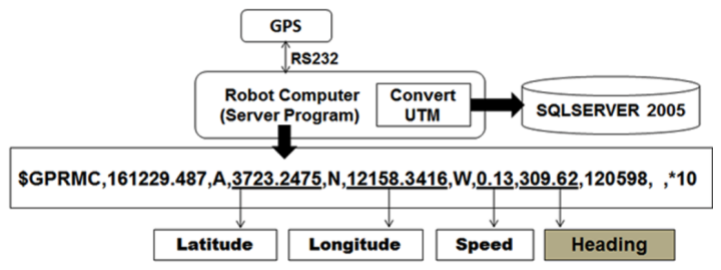
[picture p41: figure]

Figure 8. GPS data collection
A waypoint is the term used to describe a reference point for robot navigation. It includes destination latitude and longitude data. In this study, waypoints stored previously
Status | Motor Sign (MS) | Joystick sign (JS) | Proportioning
Motor Forward | !A00 – 7F | 32769 - 65536 | HEX(100 - FIX(JS / 330)) + 16
Motor Reverse | !a00 – 7F | 0 - 32767 | HEX(100 + (FIX(JS / 330) * -1)) - 16
Motor Stop | !A00 or !a00 | 32768 | 0
Table 3. Conversation table between joystick and motor controller

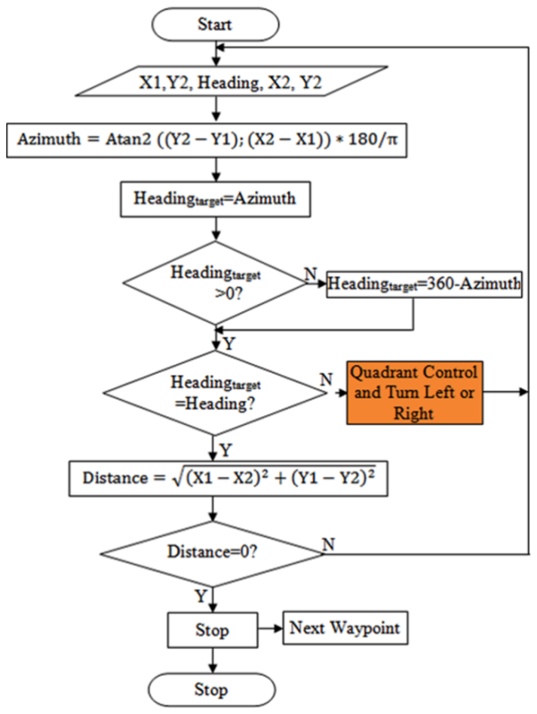
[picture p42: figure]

in the database were used for point-to-point steering in autonomous robot guidance. Two important angles called heading and azimuth angles were used to steer the robot autonomously. The heading angle was an angle between North (true or magnetic) and the current direction of the longitudinal axis of a robot in the horizontal plane. It was continuously received from the GPS receiver by the robot program. The azimuth was an angle between North and the destination point. It was continuously calculated by the robot program with Equation 7. The distance between the current robot location (X1, Y1) and the destination location (X2, Y2) was calculated with Equation 8.

Azimuth Atan Y Y | X X = | - | - 2 ( 2 1 ;( 2 | 1)) * 180 / ( | ) | p | (7)
( | ) ( | ) ² | 2 Distance | X X | Y Y = | - | + | - 1 | 2 | 1 2 | (8)

In Equation 7, the Atan2 function returns the four-quadrant inverse tangent of (y/x) in the range -π ≤ return_val ≤ π, using the signs of both arguments to determine the quadrant of the return value. Y and X can be real-valued, signed or unsigned scalars, vectors, matrices, or N-dimen‐ sional arrays containing fixed-point angle values in radians.
The first stage of the autonomous guidance algorithm determined the angle difference by comparing the current heading to the target azimuth. This step allowed the robot to determine what direction (left or right) it should turn. The next step determined the distance between the robot location and the target location. The robot program continuously calculates the distance and the minimum turn required. When the heading angle is equal to the azimuth angle, the robot is steered towards the destination point. When the distance is equal to zero, the robot arrives at the destination point. The autonomous robot guidance algo‐ rithm is given in Figure 9.
Quadrant control was the most important factor for minimum robot turnings. The compass dial was divided into four quadrants. Angles were measured clockwise from North. Quadrant 1 was between 0 and 90 degrees, Quad‐ rant 2 was between 90 and 180 degrees, Quadrant 3 was between 180 and 270 degrees, and Quadrant 4 was between 270 and 360 (or 0) degrees. The calculated azimuth angle (Equation 7) helped in determining the quadrant in which the target point was located. The heading angle of the robot helped in determining the quadrant in which the current point was located. The flowchart of the robot turning is given in Figure 10.

2.6 Software section
Two programs based on client/server architecture were developed to control and monitor the mobile robot. The server software was run on the robot computer (Figure 11).

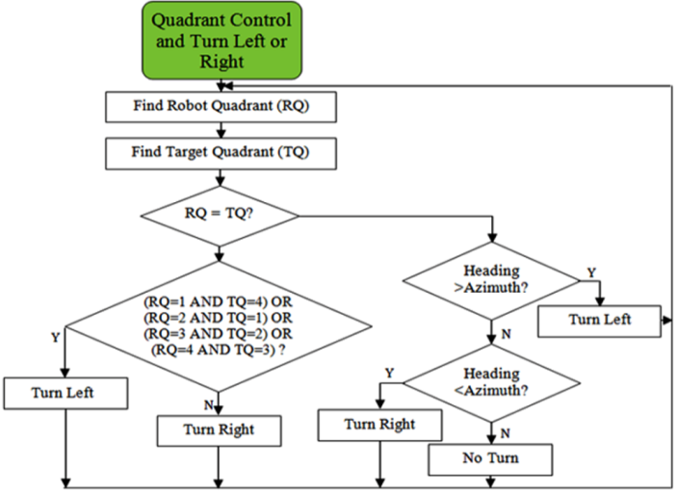
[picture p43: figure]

It was used to collect GPS data and perform steering. Collected data were stored to the database by the server program. The client program was run on the remote computer (Figure 12). It was used to manually control the robot and monitor the process data. Waypoints could be entered into the server software by the client program. In this way, a robot navigation file was created for autono‐ mous operation. The developed client/server program was written in Microsoft Visual Basic.NET 2010. The commu‐ nication between the robot and the remote computer was provided by a mobile 3G modem. The collected data were stored to a Microsoft SQL Server 2005 database.

Figure 9. Autonomous robot guidance algorithm

Figure 10. Flowchart of the robot turning

In this study, real-time video transmission to the remote computer was accomplished with a webcam camera placed on the vehicle. YawcamTM surveillance software was installed on the vehicle computer as a video server. The video server could then send the video stream from the webcam through a specific port. In the developed system, as soon as the server software sends its IP address to the client software, video streaming starts between the vehicle computer and the remote computer. The 8080 port was used to provide video streaming for both computers.

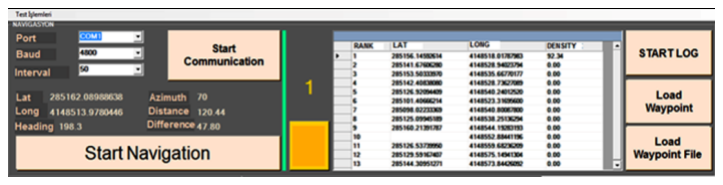
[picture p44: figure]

Figure 11. Developed server program

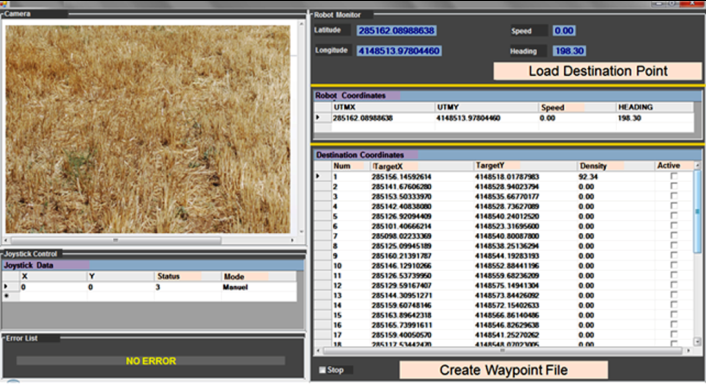
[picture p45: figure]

Figure 12. Developed client program
In the server program, the image-processing algorithm was coded for determination of stubble density. All functions of the digital camera could be controlled by both the server software and the client software. The stubble images obtained by the server software were recorded to the robot computer. The obtained stubble density data were stored into the SQL Server database.

### 3. Experimental site

The field experiments were carried out in July 2012 in the agricultural experiment field of the West Mediterranean Agricultural Research Institute in Aksu, Antalya, located in the West Mediterranean region of Turkey. The research area was located approximately 20 km from Antalya between the coordinates 30°43'21"E and 36°52'39"N. The experimental field size was 2.4 ha, with wheat planted in June 2012. The ground situation was rough and slippery because of the wheat stubble.

### 4. Results and Discussion

A test procedure comprising two phases was performed to determine the accuracy of the robot in the field. In the first phase, linear offset errors were calculated. In linear calculation, the mobile robot was steered linearly from the start point (X1, Y1) to the destination point (X2, Y2). Each straight line was approximately 100 m long. This process was conducted 10 times at constant speed. Thereafter, offset distance error was measured between the robot stop point and the destination point with the help of a tape measure (Figure 13). The result of the linear calculation is given in Table 4.

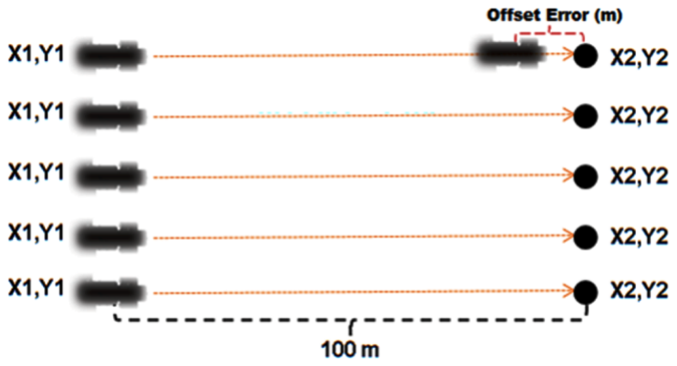
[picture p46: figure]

Figure 13. Determination of the linear offset error

Iteration Distance
(m)

Offset Error
(cm)

Mean Error
(cm)

Standard Deviation

1

100

10.30

11.32 | 0.92
2 | 11.20
3 | 10.70
4 | 10.50
5 | 12.00
6 | 11.00
7 | 13.00
8 | 12.50
9 | 10.50
10 | 11.50
Table 4. Linear offset errors

In the second phase, the mobile robot was steered autono‐ mously three times at 10 different points with different orientations relative to the destination point. Thereafter, the nonlinear offset distance error was measured between the robot stop point and the destination point with the help of a tape measure (Figure 14).
The linear offset error was found to be between 10.30 and 13 cm, and the nonlinear offset error between 13 and 20 cm. Standard deviation as calculated as 0.92 for the linear test and approximately 1.94 for the nonlinear test. The total maximum error of the robot navigation was estimated between 15 and 17 cm. The results of the nonlinear calcu‐ lations are given in Table 5.
Various studies have been done on autonomous agricul‐ tural robots and guidance systems. In [2] the authors developed an inexpensive guidance system for use on a small agricultural vehicle suitable for soil testing purposes.

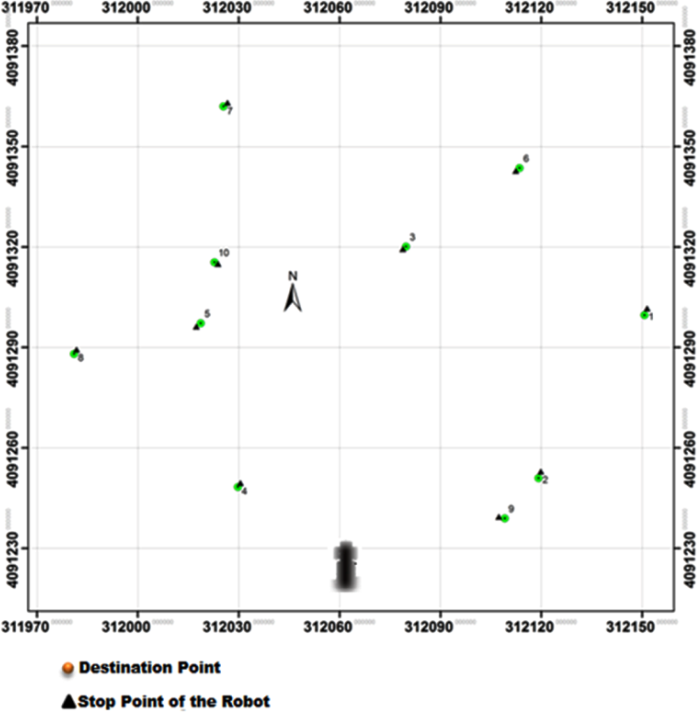
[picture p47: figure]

The paper reported that the maximum error of offsets ranged from 3 to 6 m within the actual destination point for the developed system. The study reported in [11] devel‐ oped an automated six-row rice transplanter and autono‐ mous guidance system. The paper reported that the root mean square deviation from the desired straight path was approximately 5.5 cm and the maximum deviation from the desired path is less than 12 cm at 0.7 m/s operating speed. In [26] the authors developed an algorithm for improving the multi-path error in positioning systems by coupling a differential global positioning system (DGPS) and a double electric compass (DEC) in the navigation system of an orchard robotic vehicle. The researchers reported that the average distance error of the developed system was 17.5 cm

Figure 14. Determination of nonlinear offset error

Destination
Point No.

Iteration 1
Offset
Error
(cm)

Iteration 2
Offset Error
(cm)

Iteration 3
Offset Error
(cm)
1 | 18.50 | 19.40 | 20.00
2 | 17.60 | 16.50 | 13.50
3 | 13.00 | 15.20 | 14.40
4 | 13.50 | 16.70 | 16.10
5 | 16.40 | 14.90 | 15.00
6 | 15.00 | 16.00 | 14.90
7 | 14.50 | 13.90 | 13.90
8 | 15.50 | 13.60 | 14.10
9 | 17.30 | 13.00 | 17.10
10 | 14.10 | 12.80 | 16.00
Mean Error (cm) | 15.54 | 15.20 | 15.50
Standard Dev. (cm) | 1.85 | 2.03 | 1.94
Table 5. Linear offset errors

for the straight line path and 22.3 cm for the U-turn path. The developed robot and navigation algorithm are there‐ fore very useful for precision farming applications when compared to similar studies carried out by other research‐ ers (Table 6).

Literature | Performance Results
Stombaugh et al. [27] | Lateral position error at 4.5 m/s within 16 cm (95% confidence)
Nagasaka et al. [11] | Maximum deviation from the desired path less than 12 cm
Guo and Zhang [28] | With vehicle travelling in an open field area, maximum error was reduced to 0.30 m
Nistala [2] | Total maximum error of system estimated to be between 25 and 30 cm, including the Differential GPS error
Kanjanaphachoat et al. [26] | Positioning system had an average SD of 20.7 cm and an average distance error of 17.5 cm
Garcia et al. [29] | Error usually below 1 m
Table 6. Comparison table for similar studies

In this study, the robot navigation was provided fully by RTK-GPS data. GPS accuracy is the most important factor affecting the reliability of the robot position estimates and thus the navigation of the designed robot. If a GPS receiver with different accuracy is placed on the designed robot, navigation accuracy can change significantly. Mechanical changes could be made to the robot for better performance and manoeuvrability.

### 5. Conclusions

A remote-controlled and GPS-guided autonomous robot was successfully developed for use in precision farming applications in Turkey. The developed robot can steer point to point both autonomously and manually. Both linear and nonlinear offset error measurements were made. The developed robot’s weight was 250 kg and the payload was approximately 900 kg. Because of the payload value, the robot can be used as a transport vehicle. The robot speed was approximately 3.8 km/h and the torque on each wheel was approximately 99.5 Nm. Considering these values, the developed robot can provide a high level of convenience for precision farming applications such as soil penetration measurement, soil sampling, and weed spraying. The robot can access remote computers via the internet (using a 3G modem). This makes it able to store/retrieve telemetry data to/from the remote computers. Further studies are needed to focus on adaptation of different sensors towards devel‐ oping an intelligent robot.

### 6. Acknowledgements

This work was supported by The Scientific Research Projects Coordination Unit of Akdeniz University (project number: 2011.03.0121.011).

### 7. References

[1] Andres P. Design of an autonomous navigation system for a mobile robot [thesis]. Montreal: McGill University; 2005.
[2] Nistala GJ. Development of an Inexpensive Guid‐ ance System for Agricultural Purposes [thesis]. Baton Rouge: Louisiana State University; 2006.
[3] Li M, Imou K, Wakabayashi K, Yokoyama S. Review of research on agricultural vehicle autonomous guidance. Int. J. Agric. & Biol. Eng. (IJABE). 2009;
2:1-16. | DOI: | 10.3965/j.issn.
1934-6344.2009.03.001-016
[4] Willrodt FL. Steering attachment for tractors US Patent 1506706 [Internet]. 1924. Available from: http://www.freepatentsonline.com/1506706.pdf. Accessed on 12 Jan 2015.
[5] Reid JF, Zhang Q, Noguchi N, Dickson M. Agricul‐ tural automatic guidance research in North Ameri‐ ca. Comput. Electron. Agr. 2000; 25(1-2):155-167. DOI: 10.1016/S0168-1699(99)00061-7
[6] Gerrish JB, Fehr GR, Van GR, Welch DP. Self-steering tractor guided by computer vision. Appl.
Eng. | Agric. | 1997; | 13(5):559-563. | DOI:
10.13031/2013.21641
[7] Reid JF, Searcy SW. An Algorithm for Separating Guidance Information from Row Crop Images. Trans. ASAE. 1998; 31(6):1624-1632. DOI: 10.13031/2013.30910
[8] Heraud JA, Lange AF. Agricultural automatic vehicle guidance from horses to GPS: how we got here, and where we are going. In Proceedings of the Agricultural Equipment Technology Conference; 8-11 February 2009; USA. Louisville; 2009. p. 1-67.
[9] Noguchi N, Barawid O. Robot farming system using multiple robot tractors in Japan Agriculture, Preprints of the 18th IFAC World Congress; 28 August-2 September 2011; Italy. Milan; 2011. p. 633-637.
[10] Khot LR, Tang L, Blackmore S, Nørremark N. Navigational context recognition for an autono‐ mous robot in a simulated tree plantation. Trans.
ASABE. | 2006; | | 49(5):1579-1588. | DOI:
10.13031/2013.22032
[11] Nagasaka Y, Umeda N, Kanetai Y, Taniwaki K, Sasaki Y. Autonomous guidance for rice transplant‐ ing using global positioning and gyroscopes. Comput. Electron. Agr. 2004; 43(3):223-234. DOI: 10.1016/J.COMPAG.2004.01.005
[12] Barawid Jr OC, Noguchi N. Development of low-cost and small-scale electronic robot vehicle. Automatic Guidance System in Real-time Orchard Application (Part 2). J. Soc. Agric. Machinery. 2010; 72(3):243-250. DOI: 10.11357/JSAM.72.243
[13] Bergerman M, Singh S, Hamner B. Results with autonomous vehicles operating in specialty crops.

IEEE International Conference on Robotics and Automation; 14-18 May 2012; USA. Minnesota; 2012. p. 1829-1835.
[14] Gerrish J, Surbrook T. Mobile robots in agriculture. Robotics and Intelligent Machines in Agriculture: Proceedings of the First International Conference on Robotics and Intelligent Machines in Agriculture; 2-4 October 1983; USA. St. Joseph; 1983. p. 30-41.
[15] Debain C, Chateau T, Berducat M, Martinet P, Bonton P. A guidance-assistance system for agri‐ cultural vehicles. Comput. Electron. Agr. 2000; 25:29-51. DOI: 10.1016/S0168-1699(99)00054-X
[16] Han S, Zhang Q, Noh H, Sin B. A dynamic perform‐ ance evaluation method of DGPS auto guidance systems under linear parallel-tracking applications. Trans. ASAE. 2004; 47(1):321-329. DOI: 10.13031/2013.15857
[17] Pilarski T, Happold M, Pangels H, Ollis M, Fitzpa‐ trick K, Stentz A. The demeter system for automated harvesting. Auton. Robot. 2002; 13:9-20. DOI: 10.1023/A:1015622020131
[18] Morimoto E, Suguri M, Umeda M. Vision-based navigation system for autonomous transportation vehicle. Precis. Agric. 2005; 6:239-254. DOI: 10.1007/ S11119-005-1384-X
[19] García-Pérez L, García-Alegre M, Ribeiro A. An agent of behaviour architecture for unmanned control of a farming vehicle. Comput. Electron. Agr.
2008; | 60:39-48. | DOI: | 10.1016/J.COMPAG.
2007.06.004
[20] Subramanian V, Burks T, Arroyo A. Development of machine vision and laser radar based autono‐ mous vehicle guidance systems for citrus grove navigation. Comput. Electron. Agr. 2006; 53(2): 130-143. DOI: 10.1016/J.COMPAG.2006.06.001
[21] Chen H. Robust stabilization for a class of dynamic feedback uncertain nonholonomic mobile robots with input saturation. Int. J. Control Autom. 2014; 12(6):1216-1224. DOI: 10.1007/S12555-013-0492-Z
[22] Brockett RW. Asymptotic stability and feedback stabilization. In: Brockett RW, Millman RS, Sus‐ smann HJ, editors. Differential Geometric Control Theory. Boston: Birkhauser; 1983. p.181-208.
[23] Chen H, Ding S, Chen X, Wang L, Zhu C, Chen W. Global Finite-time Stabilization for Nonholonomic Mobile Robots Based on Visual Servoing. Int. J. Adv. Robot Syst. 2014; 11(180):1-13. DOI: 10.5772/59307
[24] Chen H, Zhang J, Chen B, Li B. Global Practical Stabilization for Non-holonomic Mobile Robots with Uncalibrated Visual Parameters by Using a Switching Controller. IMA J. Math. Contr. Inform. 2013; 30:543-557. DOI: 10.1093/IMAMCI/DNS044
[25] Topakci M, Unal I, Canakci M, Celik HK, Karayel
D. Design of a Horizontal Penetrometer for Meas‐

uring On-the-Go Soil Resistance. Sensors. 2010; 10:9337-9348. DOI: 10.3390/S101009337
[26] Kanjanaphachoat C, Hsieh KC, Cheng CT, Mins-Shi
H. Combining a differential positioning system and double electric compass to improve multi-path error correction for a high-precision agricultural robotic vehicle. Maejo Int. J. Sci. Technol. 2011; 5(2): 169-180. WOS: 000298040700001
[27] Stombaugh TS, Benson ER, Hummel JW. Guidance Control of Agricultural Vehicles at High Field Speeds. Transactions of the ASAE. 1999; 42(2): 537-544. DOI: 10.13031/2013.13387
[28] Guo LS, Zhang Q. A low-cost navigation system for autonomous off-road vehicles. In: Proceedings of Automation Technology for Off-road Equipment Conference (ASABE); 7-8 October 2004; Japan. Kyoto; 2004. p. 107-119. DOI: 10.13031/2013.17824
[29] Garcia SA, Gil JG, Arribas JI. Evaluation of the use of low-cost GPS receivers in the autonomous guidance of agricultural tractors. Spanish Journal of Agricultural Research. 2011; 9(2):377-388. DOI: 10.5424/SJAR/20110902-088-10

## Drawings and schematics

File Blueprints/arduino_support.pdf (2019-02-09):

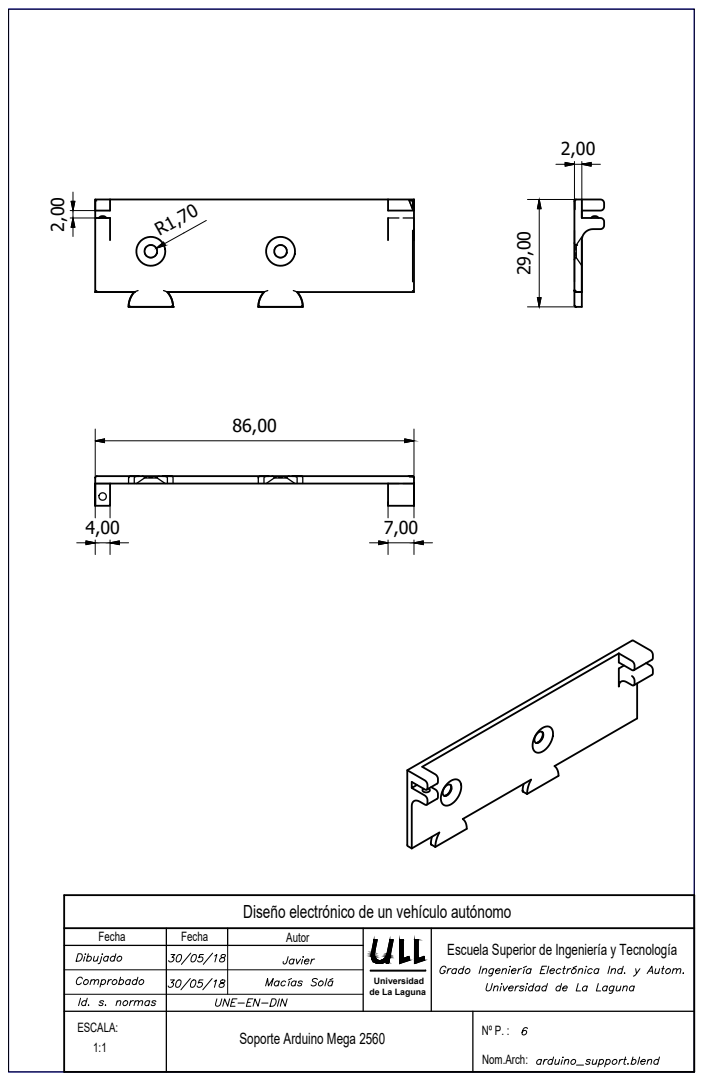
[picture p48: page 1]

Diseño electrónico de un vehículo autónomo

Escuela Superior de Ingeniería y Tecnología

Universidad
de La Laguna

Soporte Arduino Mega 2560

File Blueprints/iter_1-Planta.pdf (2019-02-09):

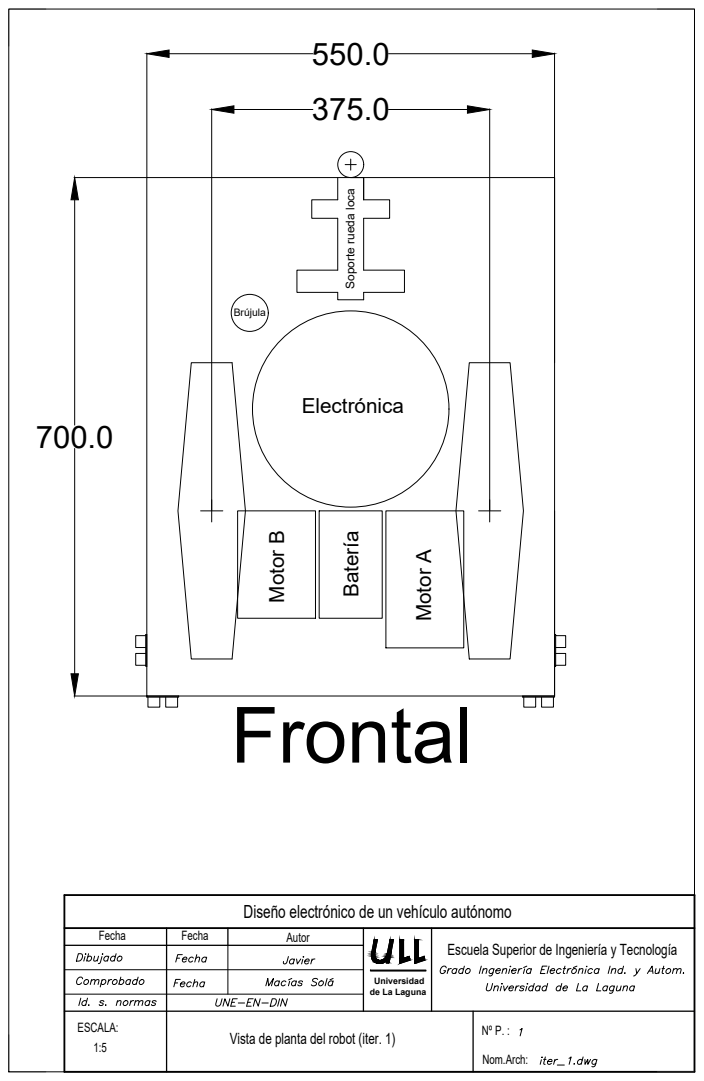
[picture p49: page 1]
Electrónica Soporte rueda loca

Motor B Batería Motor A

Diseño electrónico de un vehículo autónomo

Escuela Superior de Ingeniería y Tecnología

Universidad
de La Laguna

Vista de planta del robot (iter. 1)

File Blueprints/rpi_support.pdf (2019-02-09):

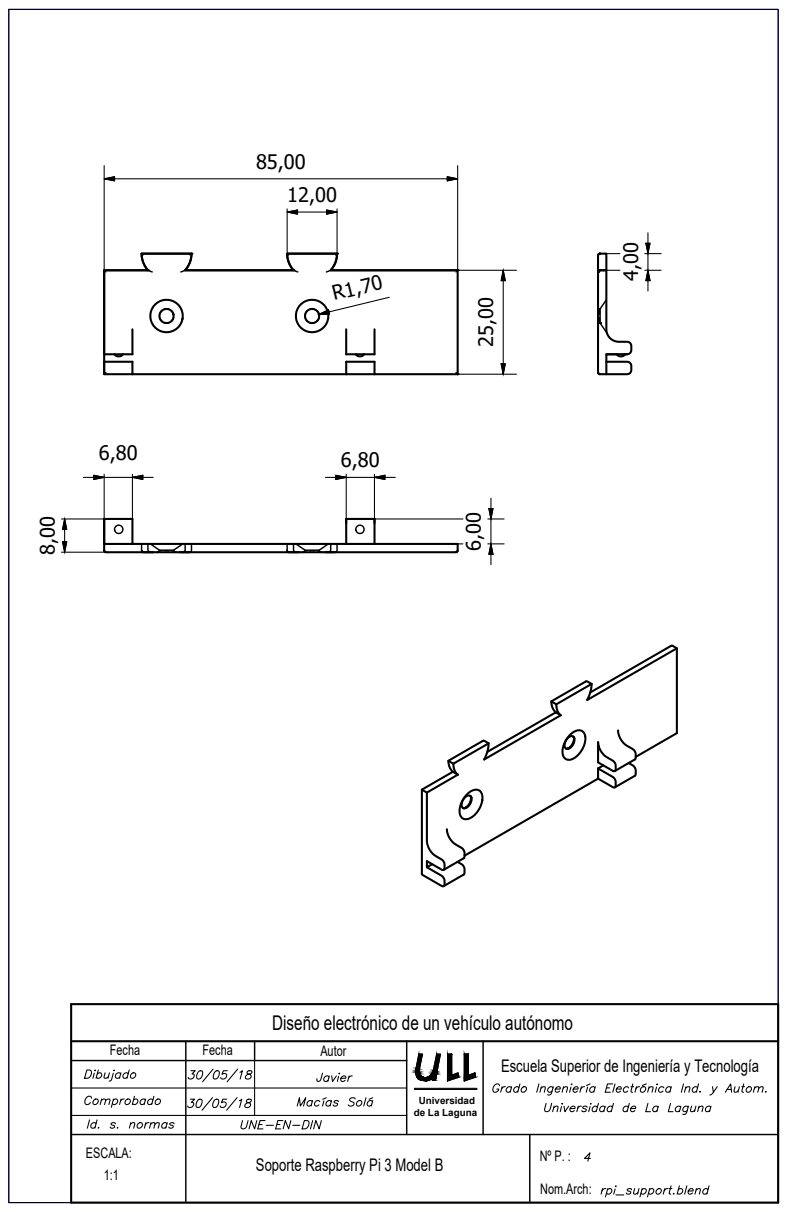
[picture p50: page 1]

Diseño electrónico de un vehículo autónomo

Escuela Superior de Ingeniería y Tecnología

Universidad
de La Laguna

Soporte Raspberry Pi 3 Model B

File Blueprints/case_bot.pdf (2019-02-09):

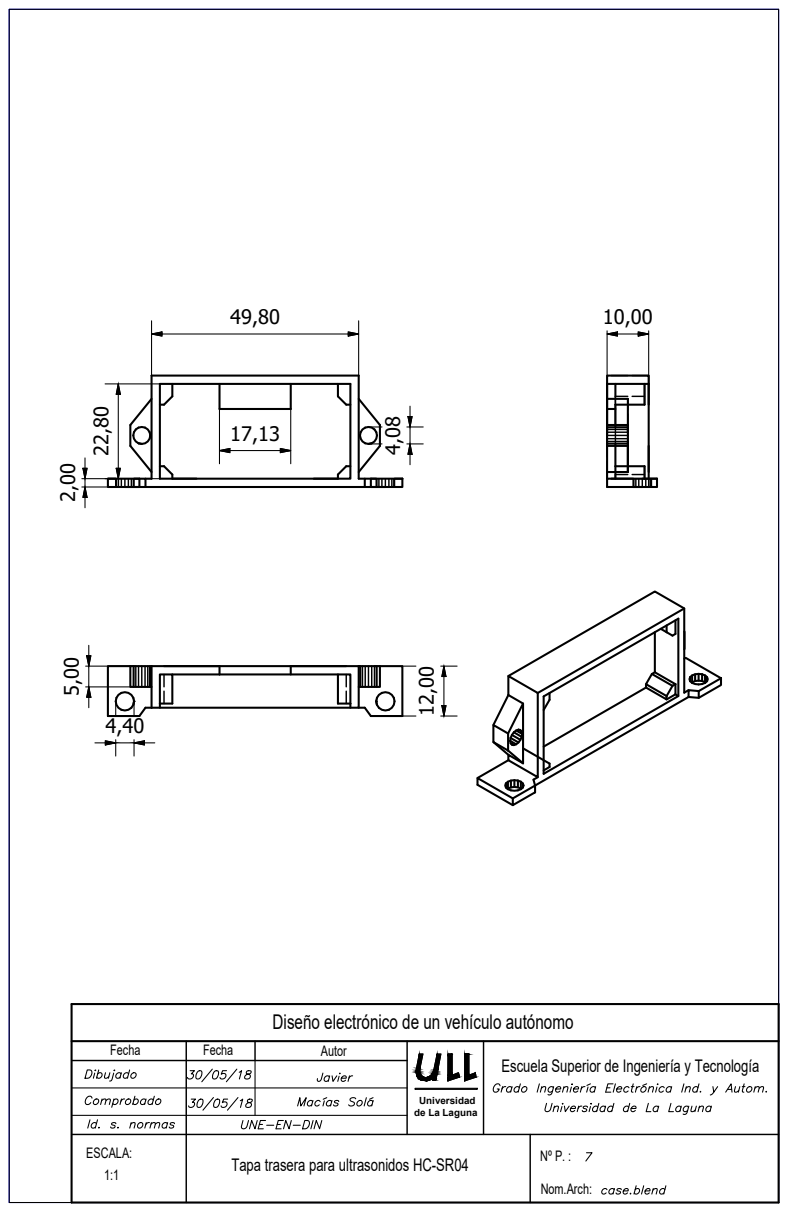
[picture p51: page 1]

Diseño electrónico de un vehículo autónomo

Escuela Superior de Ingeniería y Tecnología

Universidad
de La Laguna

Tapa trasera para ultrasonidos HC-SR04

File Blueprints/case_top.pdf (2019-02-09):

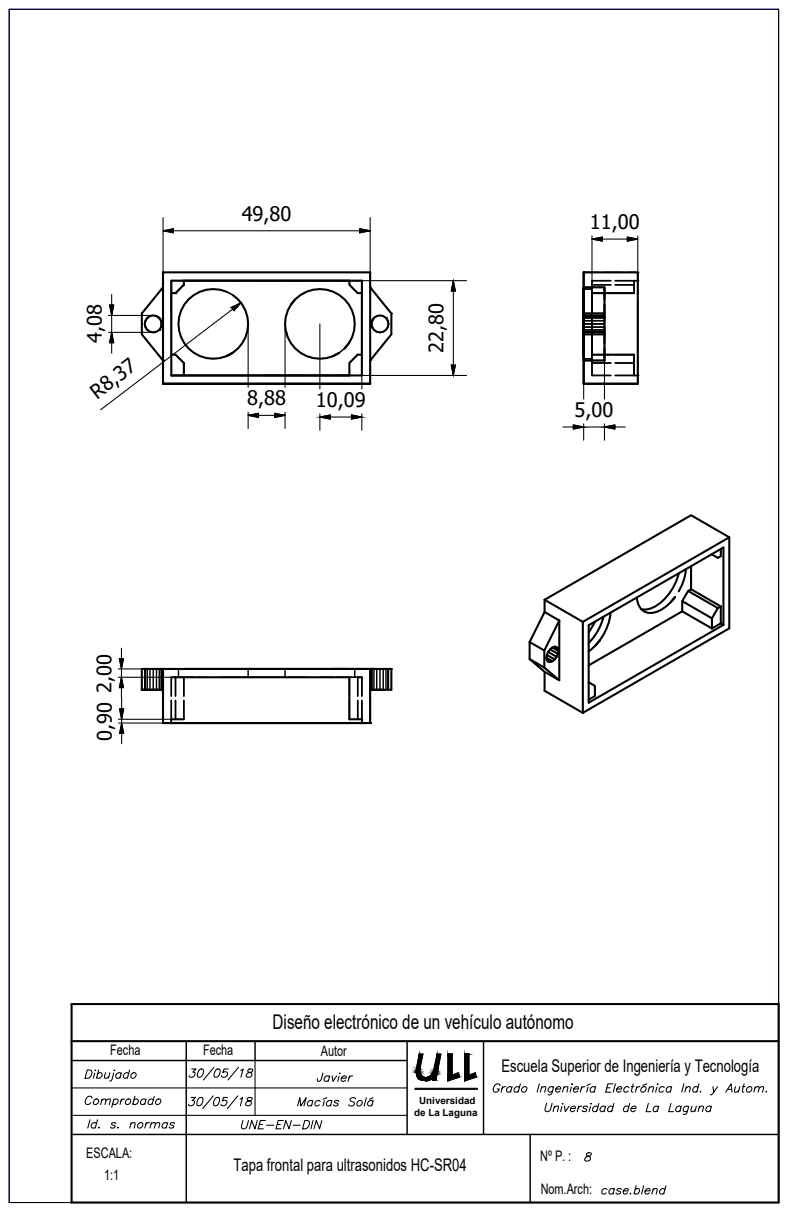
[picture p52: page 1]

Diseño electrónico de un vehículo autónomo

Escuela Superior de Ingeniería y Tecnología

Universidad
de La Laguna

Tapa frontal para ultrasonidos HC-SR04

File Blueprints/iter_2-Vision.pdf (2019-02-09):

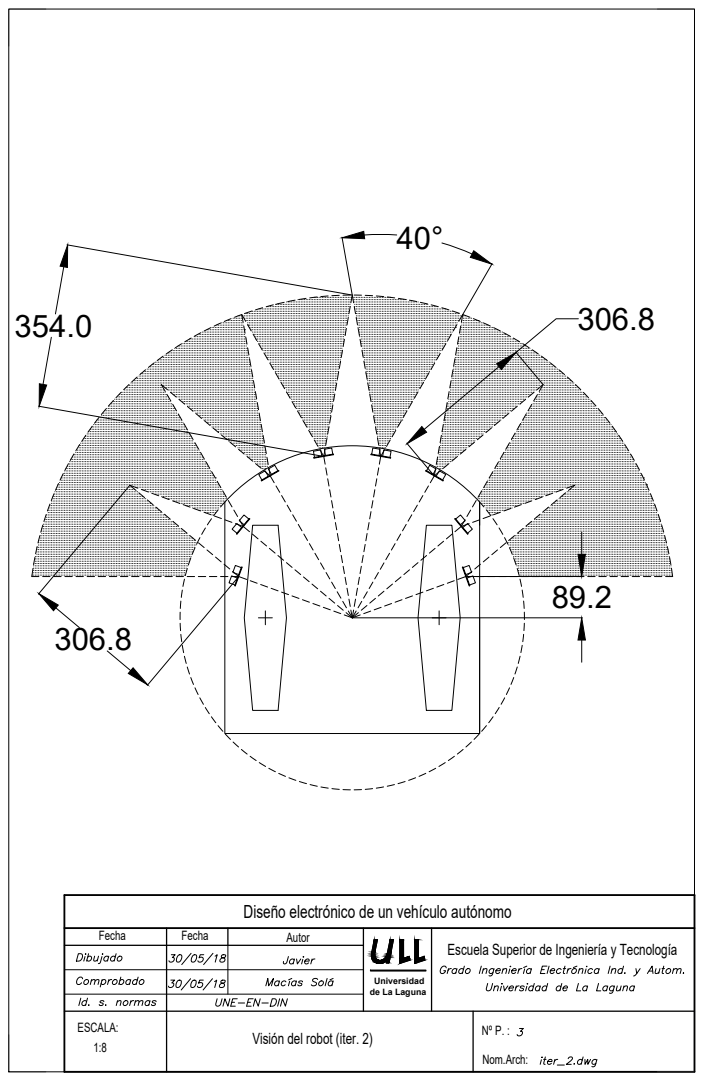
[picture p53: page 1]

Diseño electrónico de un vehículo autónomo

Escuela Superior de Ingeniería y Tecnología

Universidad
de La Laguna

Visión del robot (iter. 2)

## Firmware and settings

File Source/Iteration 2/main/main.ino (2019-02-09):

/*
main.ino is the main control sketch of GFE iteration 2.

An enable has been configured to wait for RPi to be fully booted. Using the
alias it is possible to enable/disable and change the control mode via SSH.
The manual mode is programmed to be controlled locally. Make sure to connect the
joystick to the DA-15 connector. Otherwise, expect noise and weird movements.
The automatic mode is based on the bubble rebound obstacle avoidance algorithm
for mobile robots article, published by IOAN SUSNEA, VIOREL MINZU and
GRIGORE VASILIU.

Modules implemented:
 - Motors (IMS-1 modules)
 - HC-SR04 (ultrasonic sensors)
 - HMC5883L (magnetometer - GY-273)
 - GY-GPS6MV2 (GPS module)
 - RPi control pins

Author: Javier Macias
*/

//----Importing libraries----//
#include <MOTOR.h> // Controlling motors with IMS-1 driver modules
#include <Arduino.h> // Libraries for compass HMC5883L
#include <Wire.h> // I2C library
#include <HMC5883L_Simple.h> // Compass library
#include <TinyGPS.h> // GPS library

// Create a compass
HMC5883L_Simple Compass;

// Only need to define two ultrasonic sensor pins.
const int EchoPin_0 = 24;
const int TriggerPin_0 = 25;

//----Robot parameters----//
const int L = 0.375; // Axle length (meters)


const int threshold = 60; // Centimeters of safe zone
const float heading_threshold = 5; // Degrees of tolerance
unsigned long lastTime = 0; // Used to store execution time of loop

// Variables related to GPS
float latitude, longitude;
unsigned long fix_age;
float latitude_command = 0;
float longitude_command = 0;
// Goal heading
// int heading_command = 110;
int heading_command = 170;

// Create a GPS
TinyGPS gps;

// Defining high-level control pins
const int enable_pin = 48;
const int mode_pin = 49;
bool enable = false; // Enable = 1; Disable = 0 if RPi is not ready
bool mode = false; // Manual = 0 (default); Automatic = 1

// Defining joystick inputs
int x_axis = 0; //Blue
int y_axis = 1; //Green
int z_axis = 2; //Yellow

const int button1 = 7; //White
const int button2 = 6; //Brown

int x_val = 0;
int y_val = 0;
int z_val = 0;
int button1_state = 0;
int button2_state = 0;

const int centre = 1024/2;

const int motors_wait = 10; //Wait for motors to move

// List of waypoints to follow
float waypoints[3][2] = {{1.111111, -1.111111}, {2.222222, -2.22222}, {3.333333, -3.333333}};

// Declaring controller variables
float lastEps = 0;
int lastCommand = 0;
float lastHeading = 0;

void setup(){
    Serial.begin(115200);
    //Initialize GPS communication
    Serial1.begin(9600);
    Serial.println("main.ino");

    // Initializing motor drivers
    motor.begin();
    /**
    NOTE:
    motor.begin() will change the prescaller of the timer0,
    so the arduino function delay() millis() and micros() are
    8 times slow than it should be.
    Please use motor_delay(), motor_millis(), motor_micros() instead them.
    */

    // Configuring HC-SR04 pins
    for(int i = 0; i < 8; i++){
        // Iterate through every sensor. Every two, next sensor EchoPin and TriggerPin.
        pinMode(EchoPin_0 + (2 * i), INPUT);
        pinMode(TriggerPin_0 + (2 * i), OUTPUT);
        delay(1); // Stabilization
    }

    // Initializing compass
    Wire.begin();
    Compass.SetDeclination(-4, 56, 'W'); // La Laguna
    Compass.SetSamplingMode(COMPASS_SINGLE);
    Compass.SetScale(COMPASS_SCALE_130);
    Compass.SetOrientation(COMPASS_HORIZONTAL_Y_NORTH);

    // Configuring joystick buttons
    pinMode(button1, INPUT);
    pinMode(button2, INPUT);

    // Configuring high-level control pins
    pinMode(enable_pin, INPUT);
    pinMode(mode_pin, INPUT);

    // Wait until RPi is ready
    do{
        enable = digitalRead(enable_pin);
        Serial.println("Waiting for RPi to be ready...");
        motor_delay(1000); // Wait for one second
    }while(!enable);
}

void loop(){
    // Wait for robot to be enabled
    enable = digitalRead(enable_pin);
    while(!enable){
        enable = digitalRead(enable_pin);
        Serial.println("Robot is disabled...");
        motor_delay(1000); // Wait for one second
    }

    mode = digitalRead(mode_pin);
    // Enter manual mode if mode is false and robot is enabled
    while(!mode && enable){
        joystick_control();
        mode = digitalRead(mode_pin);
        enable = digitalRead(enable_pin);
    }

    // Otherwise, automatic mode
    if(mode && enable){
        do{
            get_location(gps);
            Serial.print("latitude = ");
            Serial.print((float)latitude, 6);
            Serial.print(" ");
            Serial.print("latitude = ");
            Serial.println((float)longitude, 6);
            delay(500);
        }while(latitude == 0 && longitude == 0);

        for(int i = 0; i < 3; i++){
            // Set the next waypoint
            latitude_command = waypoints[i][0];
            Serial.print("latitude_command = ");
            Serial.print((float)latitude_command, 6);
            longitude_command = waypoints[i][1];
            Serial.print(" longitude_command = ");
            Serial.println((float)longitude_command, 6);

            do{
                // Recalculate heading after each iteration
                heading_command = gps.course_to(latitude, longitude, latitude_command, longitude_command);
                Serial.print("heading_command = ");
                Serial.println(heading_command);
                automatic_mode(); //Navigate
                get_location(gps);
                Serial.print("latitude = ");
                Serial.print((float)latitude, 6);
                Serial.print(" ");
                Serial.print("latitude = ");
                Serial.println((float)longitude, 6);

                enable = digitalRead(enable_pin);
            }while(!goal_is_reached(latitude, longitude, latitude_command, longitude_command) && enable);

            // Get out if !enable
            if(!enable){
                break;
            }
        }
    }
}

// Read current position
static void get_location(TinyGPS &gps){
    while (Serial1.available()){
        int c = Serial1.read();
        if (gps.encode(c)){
            // Retrieves +/- lat/long in 100000ths of a degree
            gps.f_get_position(&latitude, &longitude, &fix_age);
        }
    }
}

// Check if current location is close enough to the objective
int goal_is_reached(float latitude, float longitude, float latitude_command, float longitude_command){
    if(abs(latitude - latitude_command) <= 0.00001 && abs(longitude - longitude_command) <= 0.00001){
        return 1;
    }
    else{
        return 0;
    }
}

// Automatic mode function
void automatic_mode(){
    // Calculate current and elapsed time for PI controller
    unsigned long now = millis();
    double timeChange = (double)(now - lastTime)/1000; //Seconds
    Serial.print("timeChange = ");
    Serial.println(timeChange);

    float heading = Compass.GetHeadingDegrees();
    Serial.print("heading = ");
    Serial.println(heading);

    unsigned int *sonar_readings;
    sonar_readings = average_read_sensors();
    for(int i = 0; i < 8; i++){
        Serial.print(sonar_readings[i]);
        Serial. print(" ");
    }

    // Obstacle avoidance algorithm
    if(check_for_obstacles(sonar_readings, 0, 8)){
        Serial.println("Obstacle detected!");

        float alpha_r = 0;
        do{
            Serial.println("Computing rebound angle...");
            alpha_r = rebound_angle(sonar_readings);
            Serial.print("alpha_r = ");
            Serial.println(alpha_r);

            Serial.println("Adjusting heading.");

            heading = Compass.GetHeadingDegrees();
            Serial.print("heading = ");
            Serial.println(heading);

            if(alpha_r < 0){
                Serial.println("alpha_r < 0. Turning left.");
                // Turn left. Equivalent to compute new heading + adjust motion in the paper.
                adjust_heading(heading, alpha_r, 1, timeChange);
            }
            else{
                Serial.println("alpha_r > 0. Turning right.");
                adjust_heading(heading, alpha_r, 0, timeChange);
            }

            recheck_obstacles:
            sonar_readings = average_read_sensors();
            for(int i = 0; i < 8; i++){
                Serial.print(sonar_readings[i]);
                Serial.print(" ");
            }
            enable = digitalRead(enable_pin);
        }while(check_for_obstacles(sonar_readings, 0, 8) && enable);

        if(!goal_visible(sonar_readings) && enable){
            Serial.println("Goal is not visible. Move forward!");
            move_forward();
            goto recheck_obstacles;
        }
    }
    else{
        // No obstacles, orientate to heading.
        if(heading >= heading_command + heading_threshold || heading <= heading_command - heading_threshold){
            do{
                if(((heading - heading_command < 0 && abs(heading - heading_command) < 180) || (heading - heading_command > 0 && abs(heading - heading_command) > 180))){
                    Serial.println("No obstacles around, turning right to heading_command!");
                    rotate_right(heading_command, timeChange);
                }
                else{
                    Serial.println("No obstacles around, turning left to heading_command!");
                    rotate_left(heading_command, timeChange);
                }
                heading = Compass.GetHeadingDegrees();
                Serial.print("heading = ");
                Serial.println(heading);
                enable = digitalRead(enable_pin);
            }while ((heading >= heading_command + heading_threshold || heading <= heading_command - heading_threshold) && enable);
        }
        else{ // Continue forward
            move_forward();
        }
    }

    lastTime = now;
}

// Rotate robot to the new heading
int adjust_heading(float heading, float alpha_r, int direction, double timeChange){
    if(direction == 1){
        // Calculate the new heading. Note: 0 for turning right, 1 for left
        float avoid_direction = calculate_heading(heading, abs(alpha_r), 1);
        Serial.print("avoid_direction = ");
        Serial.println(avoid_direction);
        do{
            rotate_left(avoid_direction, timeChange);
            heading = Compass.GetHeadingDegrees();
            Serial.print("Heading: ");
            Serial.println(heading);
            enable = digitalRead(enable_pin);
        }while((heading >= avoid_direction + heading_threshold || heading <= avoid_direction - heading_threshold) && enable);
    }
    else{
        // Calculate the new heading. Note: 0 for turning right, 1 for left
        float avoid_direction = calculate_heading(heading, abs(alpha_r), 0);
        Serial.print("avoid_direction = ");
        Serial.println(avoid_direction);
        do{
            rotate_right(avoid_direction, timeChange);
            heading = Compass.GetHeadingDegrees();
            Serial.print("Heading: ");
            Serial.println(heading);
            enable = digitalRead(enable_pin);
        }while((heading >= avoid_direction + heading_threshold || heading <= avoid_direction - heading_threshold) && enable);
    }
}

// Check if goal is visible.
int goal_visible(unsigned int *sonar_readings){
    float heading = Compass.GetHeadingDegrees();

    float right_limit = calculate_heading(heading, 90, 0);
    float left_limit = calculate_heading(heading, 90, 1);

    // The goal is on the right side.
    if(heading_command > heading  && heading_command < right_limit){
        Serial.println("Checking obstacles on the right");
        if(search_goal(sonar_readings, 0, 4)){
            Serial.println("Goal was found on the right");
            return 0;
        }
        else{
            return 1; // Raise error if goal is not visible
        }
    }
    else{ // The goal is on the left side.
        Serial.println("Checking obstacles on the left");
        if(search_goal(sonar_readings, 4, 8)){
            Serial.println("Goal was found on the left");
            return 0;
        }
        else{
            return 1; // Raise error if goal is not visible
        }
    }
}

// See if goal is visible from the given sensors
int search_goal(unsigned int *sonar_readings, const int start, const int end){
    unsigned int goal_boundary[8] = {50, 50, 50, 60, 60, 50, 50, 50}; // Centimeters

    for(int i = start; i < end; i++){
        if(sonar_readings[i] <= goal_boundary[i]){
            return 1; // Raise error if goal is not found
        }
    }
    return 0;
}

// Filter sensor readings by doing the average
unsigned int *average_read_sensors(){
    unsigned int sum[8] = {0}; //Initialize to zero.
    static unsigned int average[8] = {0}; //Initialize to zero.
    unsigned int *sonar_readings;

    for(int j = 0; j < 2; j++){
        sonar_readings = read_sensors();
        for(int i = 0; i < 8; i++){
            sum[i] += sonar_readings[i];
        }
    }

    for(int k = 0; k < 8; k++){
        average[k] = sum[k]/2;
    }

    return average;
}

// Store ultrasonic sensor readings. Sequence: 0 3 6 1 4 7 2 5
unsigned int *read_sensors(){
    static unsigned int sonar_readings[8] = {0}; //Initialize to zero.
    int i = 0;
    int cont = 0;
    while(cont < 8){
        sonar_readings[i] = calculate_distance(TriggerPin_0 + (2 * i), EchoPin_0 + (2 * i));
        if(cont == 2){
            i = 1;
        }
        else if(cont == 5){
            i = 2;
        }
        else{
            i += 3;
        }
        cont++;
        delay(10); // 10 ms delay to avoid false positives
    }
    return sonar_readings;
}

// Compute rebound angle
float rebound_angle(unsigned int *sonar_readings){
    const float alpha_0 = 180/8;
    float num = 0;
    float den = 0;
    for(int i = -4; i < 5; i++){
        if(i == 0){ // Zero is not taken.
            i = 1;
        }

        float alpha_i = i * alpha_0;

        num += alpha_i * sonar_readings[i];
        den += sonar_readings[i];
    }

    float alpha_r = num/den;

    return alpha_r;
}

// Compare whether any reading is below threshold
int check_for_obstacles(unsigned int *sonar_readings, const int start, const int end){
    unsigned int bubble_boundary[8] = {20, 20, 30, 40, 40, 30, 20, 20}; // Centimeters

    for(int i = start; i < end; i++){
        if(sonar_readings[i] <= bubble_boundary[i]){
            return 1;
        }
    }
    return 0;
}

// Read the distance of an ultrasonic sensor. Raw output, unfiltered.
int calculate_distance(const int TriggerPin, const int EchoPin){
    long duration, distanceCm;

    digitalWrite(TriggerPin, LOW);  //Setting to LOW for 4us for cleaner reading
    delayMicroseconds(4);
    digitalWrite(TriggerPin, HIGH);  //Triggering for 10us
    delayMicroseconds(10);
    digitalWrite(TriggerPin, LOW);

    duration = pulseIn(EchoPin, HIGH);  //Measuring the time between pulses in microseconds

    distanceCm = duration * 10 / 292 / 2;   //Converting to cm

    return distanceCm;
}

// Used to calculate proper heading values
float calculate_heading(float heading, float alpha_r, int direction){
    if(direction == 0){
        if(heading + alpha_r > 360){
            return heading + alpha_r - 360;
        }
        else{
            return heading + alpha_r;
        }
    }
    else{
        if(heading - alpha_r < 0){
            return heading - alpha_r + 360;
        }
        else{
            return heading - alpha_r;
        }
    }
}

// PI controller for rotation of the robot
int calculate_command(float goal, double timeChange){
    float heading = Compass.GetHeadingDegrees();
    float eps = abs(heading - goal);
    float deltaPV = abs(heading - lastHeading);

    // Kp and Ti manually adjusted
    int Kp = 4;
    int Ti = 2;
    float max_command = 130;

    float command = (Kp * (deltaPV + 1/Ti * (eps * timeChange)) + lastCommand) * (max_command/180);

    // Clamp to avoid values over max_command due to excessive error/gain
    command = constrain(command, 60, max_command);

    lastEps = eps;
    lastCommand = command;
    lastHeading = heading;

    return command;
}

// Rotate left
void rotate_left(float goal, double timeChange){
    Serial.println("Rotating left!");
    float command = calculate_command(goal, timeChange);
    motor.set(A, command, REVERSE);
    motor.set(B, command, FORWARD);
    motor_delay(10);
}

// Rotate right
void rotate_right(float goal, double timeChange){
    Serial.println("Rotating right!");
    float command = calculate_command(goal, timeChange);
    motor.set(A, command, FORWARD);
    motor.set(B, command, REVERSE);
    motor_delay(10);
}

// Move forward
void move_forward(){
    Serial.println("Going forward! @ open space");
    motor.set(A, 120, FORWARD); // Drift correction
    motor.set(B, 130, FORWARD);
    motor_delay(10);
}

void joystick_control(){
    //Read, store and correct raw values from joystick
    x_val = calculate_average(x_axis);
    Serial.print("x_val = ");
    Serial.println(x_val);
    y_val = calculate_average(y_axis);
    Serial.print("y_val = ");
    Serial.println(y_val);
    // For some reason z_axis is not working.
    // z_val = calculate_average(z_axis);
    // Serial.print("z_val = ");
    // Serial.println(z_val);
    button1_state = digitalRead(button1);
    button2_state = digitalRead(button2);

    x_val = 1024 - x_val;
    y_val = 1024 - y_val;

	int x = x_val - centre;
	int y = y_val - centre;

    // Computing speed and direction in function of joystick position
    //	Convert to polar coordinates
   	float r = hypot(x, y);
   	float t = atan2(y, x);

    //	Rotate by 45 degrees
   	t = t - 3.14159265358979323846 / 4;

    //  Back to cartesian
    float left = r * cos(t);
    float right = r * sin(t);

    //  Rescale the new coords
    left = left * sqrt(2);
    right = right * sqrt(2);

    //  Clamp to -245/+245 to avoid over power
    left = fmax(-245, fmin(left, 245));
    right = fmax(-245, fmin(right, 245));

    float left_abs = abs(left);
    float right_abs = abs(right);

    // Controlling the motors
    if(button2_state == 0 || (x <= 100 && x >= -100 && y <= 100 && y >= -100)){
        Serial.println("Stop!");
        motor.set(A, 0, FORWARD);
        motor.set(B, 0, FORWARD);
        motor_delay(motors_wait);
    }
    else{
        if(y > 0){
            if(left > 0 && right > 0){
                motor.set(A, left, FORWARD);
                motor.set(B, right, FORWARD);
                motor_delay(motors_wait);
            }
            else if(left > 0 && right < 0){
                motor.set(A, left, FORWARD);
                motor.set(B, right_abs, REVERSE);
                motor_delay(motors_wait);
            }
            else if(left < 0 && right > 0){
                motor.set(A, left_abs, REVERSE);
                motor.set(B, right, FORWARD);
                motor_delay(motors_wait);
            }
        }
        else{
            if(left < 0 && right < 0){
                motor.set(A, right_abs, REVERSE);
                motor.set(B, left_abs, REVERSE);
                motor_delay(motors_wait);
            }
            else if(left > 0 && right < 0){
                motor.set(A, right_abs, REVERSE);
                motor.set(B, left, FORWARD);
                motor_delay(motors_wait);
            }
            else{
                motor.set(A, right, FORWARD);
                motor.set(B, left_abs, REVERSE);
                motor_delay(motors_wait);
            }
        }
    }
}

// Calculate average of analog values
int calculate_average(int axis){
    int value = 0;
    int num = 10;
    for(int i = 0; i < num; i++){
        value += analogRead(axis);
    }
    int average = value/num;

    return average;
}

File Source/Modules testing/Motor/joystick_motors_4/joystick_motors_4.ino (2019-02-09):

/**
  @file       MotorDemo
  @author     ELECHOUSE
  @version    V0.1
  @date       2012-6-22
  @brief        50A-DualChannelMotorDriverBoard demo code.
  @URL https://github.com/elechouse/motor
*/

/** import motor library */
#include <MOTOR.h>
#include <stdio.h>
#include <stdlib.h>
#include <WiFiEsp.h>
#include <WiFiEspUdp.h>

// Defining joystick inputs
const int x_axis = 1; //Blue
const int y_axis = 2; //Green
const int z_axis = 4; //Yellow

const int button1 = 5; //Marrón
const int button2 = 6; //Blanco

char ssid[] = "ESP8266 Server";         // your network SSID (name)
char pass[] = "esp8266server";        // your network password
int status = WL_IDLE_STATUS;     // the Wifi radio's status

unsigned int localPort = 10002;  // local port to listen on

char packetBuffer[255];          // buffer to hold incoming packet

int x_val = 0;
int y_val = 0;
int z_val = 0;
int button1_state = 0;
int button2_state = 0;

const int centre = 1024/2;

WiFiEspUDP Udp;

void setup(void){
    Serial.begin(115200);   // initialize serial for debugging
    Serial.println("joystick_motors_4.ino");

    Serial2.begin(9600);    // initialize serial for ESP module
    WiFi.init(&Serial2);    // initialize ESP module

    // check for the presence of the shield
    if(WiFi.status() == WL_NO_SHIELD){
      Serial.println("WiFi shield not present");
      while (true); // don't continue
    }

    Serial.print("Attempting to start AP ");
    Serial.println(ssid);

    // uncomment these two lines if you want to set the IP address of the AP
    //IPAddress localIp(192, 168, 111, 111);
    //WiFi.configAP(localIp);

    // start access point
    status = WiFi.beginAP(ssid, 10, pass, ENC_TYPE_WPA2_PSK);

    Serial.println("Access point started");
    printWifiStatus();

    Serial.println("\nStarting connection to server...");
    // if you get a connection, report back via serial:
    Udp.begin(localPort);

    Serial.print("Listening on port ");
    Serial.println(localPort);

    /** motor driver initialize */
    motor.begin();
    /**
    NOTE:
    motor.begin() will change the prescaller of the timer0,
    so the arduino function delay() millis() and micros() are
    8 times slow than it should be.
    Please use motor_delay(), motor_millis(), motor_micros() instead them.
    */
}


void loop(void){
    x_val = 512;
    y_val = 512;
    z_val = 512;
    button1_state = 1;
    button2_state = 1;

    // if there's data available, read a packet
    int packetSize = Udp.parsePacket();
    if(packetSize){
        Serial.print("Received packet of size ");
        Serial.println(packetSize);
        Serial.print("From ");
        IPAddress remoteIp = Udp.remoteIP();
        Serial.print(remoteIp);
        Serial.print(", port ");
        Serial.println(Udp.remotePort());

        // read the packet into packetBufffer
        int len = Udp.read(packetBuffer, 255);
        if (len > 0){
            packetBuffer[len] = 0;
        }
        Serial.println("Contents:");
        Serial.println(packetBuffer);

        // Message to decode i.e. 1023 1023 1023 1 1
        sscanf(packetBuffer,"%d %d %d %d %d %d", &x_val, &y_val, &z_val, &button1_state, &button2_state);

        Serial.print("x_val = ");
        Serial.println(x_val);
        Serial.print("y_val = ");
        Serial.println(y_val);
        Serial.print("z_val = ");
        Serial.println(z_val);
        Serial.print("button1_state = ");
        Serial.println(button1_state);
        Serial.print("button2_state = ");
        Serial.println(button2_state);
    }

    x_val = 1024 - x_val;
    Serial.print("x_val = ");
    Serial.println(x_val);
    y_val = 1024 - y_val;
    Serial.print("y_val = ");
    Serial.println(y_val);

	int x = x_val - centre;
    Serial.print("x = ");
    Serial.println(x);
	int y = y_val - centre;
    Serial.print("y = ");
    Serial.println(y);

    // Computing the speed
    //	convert to polar
   	float r = hypot(x, y);
   	float t = atan2(y, x);

//	rotate by 45 degrees
   	t = t - 3.14159265358979323846 / 4;

//  back to cartesian
    float left = r * cos(t);
    float right = r * sin(t);

//  rescale the new coords
    left = left * sqrt(2);
    right = right * sqrt(2);

//  clamp to -245/+245 to avoid over power
    left = fmax(-245, fmin(left, 245));
    right = fmax(-245, fmin(right, 245));
    Serial.print(left);
    Serial.print(" ");
    Serial.println(right);

    float left_abs = abs(left);
    float right_abs = abs(right);
    Serial.print(left_abs);
    Serial.print(" ");
    Serial.println(right_abs);

    if(button1_state == 0 || x <= 100 && x >= -100 && y <= 100 && y >= -100){
        Serial.println("Stop!");
        motor.set(A, 0, FORWARD);
        motor.set(B, 0, FORWARD);
        motor_delay(150);
    }

    else{
        if(y >= 0){
            Serial.println("y > 0");
            if(left < 0){
                Serial.print("Motor left moving REVERSE @ ");
                Serial.println(left_abs);
                motor.set(A, left_abs, REVERSE);
                motor_delay(75);
            }
            else{
                Serial.print("Motor left moving FORWARD @ ");
                Serial.println(left);
                motor.set(A, left, FORWARD);
                motor_delay(75);
            }
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
